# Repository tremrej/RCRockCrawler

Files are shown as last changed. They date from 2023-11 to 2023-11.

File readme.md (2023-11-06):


# RockCrawler
This is a remix version of an RC Rock Crawler that I found on Thingiverse.
The original model got deleted since then. So I included the original here.
The remix was first publish in Thingiverse at [Remix Rc Rock Crawler, new gearbox](https://www.thingiverse.com/thing:5236263).
I modified the gearbox to make it slower, hence with more torque.

General instruction:

1. Make sure the printer is well calibrated. Specifically the extruder. The extrusion factor, also know as the extrusion multiplier, will have a big impact on the way the pieces fits together. I personnaly use that guide before using a new filament: [Extrusion Multiplier](https://ellis3dp.com/Print-Tuning-Guide/articles/extrusion_multiplier.html)
2. Print every pieces in PLA.
3. Print the shock in PETG to get more flexibility.
4. If you decide to print the tires print them in TPU, the softest one you can find. The grip is not very good with printed tires. For better grip you can buy the tires. In that case print the wheel part wheel_26_5mm.stl.
4. If the screws tend to break the plastic part you can enlarge the hole with a drill bit.
4. Use plenty of light grease in the gear box
5. Use a bit of light grease in the wheel hub.
6. If the center drive shaft keep falling off you can print this longer one: Center_Drive_Shaft_P2_15.55mm.stl.
7. I provided a longer shock shock_46mm_stl. The short version tend to keep the car a bit low.

Video:

1. [In action](https://youtu.be/3EBpf9YP5C4)
2. [Showing the shock](https://youtu.be/YSYngEb9dG8)
3. [Gearbox assembly](https://youtu.be/KAkp_eB5qdQ)

I found a link to the original video from the original designer:

1. [Make an RC Rock Crawler - Part 1](https://www.youtube.com/watch?v=WgZuojB2sF8&t=138s)
2. [Make an RC Rock Crawler - Part 2](https://www.youtube.com/watch?v=jjvKoB2oO8Q&t=319s)

Documentation generated by the OpenSCAD library [NopSCADlib](https://github.com/nophead/NopSCADlib/tree/master).

License: [Creative Commons - Attribution - Share Alike](https://creativecommons.org/licenses/by-sa/3.0/).

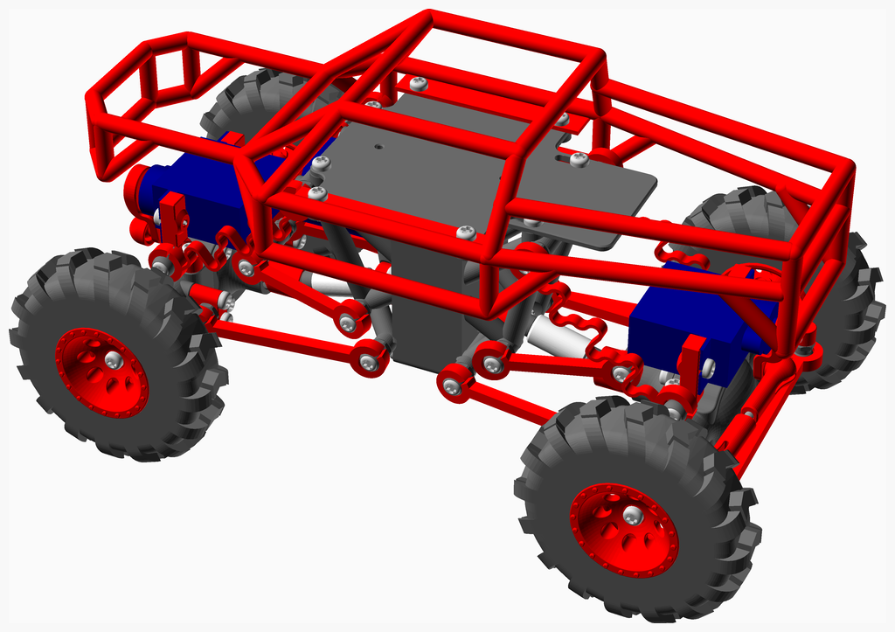
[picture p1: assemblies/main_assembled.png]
Main Assembly


<span></span>

---
## Table of Contents
1. [Parts list](#Parts_list)
1. [Wheel Left Assembly](#wheel_left_assembly)
1. [Wheel Right Assembly](#wheel_right_assembly)
1. [Drive Shaft Assembly](#drive_shaft_assembly)
1. [Servo Control Link Assembly](#Servo_control_link_assembly)
1. [Hub R Assembly](#Hub_R_assembly)
1. [Hub L Assembly](#Hub_L_assembly)
1. [Axle Part1 1 R Assembly](#Axle_part1_1_R_assembly)
1. [Axle Part1 1 L Assembly](#Axle_part1_1_L_assembly)
1. [G34 Assembly](#G34_assembly)
1. [Axle Part1 Assembly](#Axle_part1_assembly)
1. [Axle Part2 Assembly](#Axle_part2_assembly)
1. [Axle Part3 Assembly](#Axle_part3_assembly)
1. [Axle Part4 Assembly](#Axle_part4_assembly)
1. [Axle Part5 Assembly](#Axle_part5_assembly)
1. [Axle Part6 Assembly](#Axle_part6_assembly)
1. [Axle Part7 Assembly](#Axle_part7_assembly)
1. [Axle Final Assembly](#Axle_final_assembly)
1. [GearBox Part1 Assembly](#gearBox_part1_assembly)
1. [GearBox Part2 Assembly](#gearBox_part2_assembly)
1. [GearBox Part3 Assembly](#gearBox_part3_assembly)
1. [GearBox Part4 Assembly](#gearBox_part4_assembly)
1. [GearBox Part5 Assembly](#gearBox_part5_assembly)
1. [GearBox Part6 Assembly](#gearBox_part6_assembly)
1. [GearBox Part7 Assembly](#gearBox_part7_assembly)
1. [GearBox Final Assembly](#gearBox_final_assembly)
1. [Suspension Part1 Assembly](#suspension_part1_assembly)
1. [Suspension Part2 Assembly](#suspension_part2_assembly)
1. [Main Assembly](#main_assembly)

<span></span>
[Top](#TOP)

---

## Parts list
| <span style="writing-mode: vertical-rl; text-orientation: mixed;">2 x Axle&nbsp;Final</span> | <span style="writing-mode: vertical-rl; text-orientation: mixed;">GearBox&nbsp;Final</span> | <span style="writing-mode: vertical-rl; text-orientation: mixed;">Main</span> | <span style="writing-mode: vertical-rl; text-orientation: mixed;">TOTALS</span> |  |
|---:|---:|---:|---:|:---|
|  |  |  | | **Vitamins** |
| &nbsp;&nbsp;8&nbsp; | &nbsp;&nbsp;.&nbsp; | &nbsp;&nbsp;.&nbsp; |  &nbsp;&nbsp;8&nbsp; | &nbsp;&nbsp; Ball bearing MR128-2RS 8mm x 12mm x 3.5mm |
| &nbsp;&nbsp;6&nbsp; | &nbsp;&nbsp;2&nbsp; | &nbsp;&nbsp;.&nbsp; |  &nbsp;&nbsp;8&nbsp; | &nbsp;&nbsp; Ball bearing MR63ZZ 5mm x 8mm x 2.5mm |
| &nbsp;&nbsp;16&nbsp; | &nbsp;&nbsp;4&nbsp; | &nbsp;&nbsp;.&nbsp; |  &nbsp;&nbsp;20&nbsp; | &nbsp;&nbsp; Screw M2 pan self tap x  5mm |
| &nbsp;&nbsp;18&nbsp; | &nbsp;&nbsp;8&nbsp; | &nbsp;&nbsp;4&nbsp; |  &nbsp;&nbsp;30&nbsp; | &nbsp;&nbsp; Screw M2 pan self tap x  6mm |
| &nbsp;&nbsp;4&nbsp; | &nbsp;&nbsp;.&nbsp; | &nbsp;&nbsp;4&nbsp; |  &nbsp;&nbsp;8&nbsp; | &nbsp;&nbsp; Screw M2 pan self tap x  8mm |
| &nbsp;&nbsp;14&nbsp; | &nbsp;&nbsp;12&nbsp; | &nbsp;&nbsp;.&nbsp; |  &nbsp;&nbsp;26&nbsp; | &nbsp;&nbsp; Screw M2 pan self tap x 10mm |
| &nbsp;&nbsp;10&nbsp; | &nbsp;&nbsp;4&nbsp; | &nbsp;&nbsp;.&nbsp; |  &nbsp;&nbsp;14&nbsp; | &nbsp;&nbsp; Screw M2 pan self tap x 12mm |
| &nbsp;&nbsp;.&nbsp; | &nbsp;&nbsp;1&nbsp; | &nbsp;&nbsp;.&nbsp; |  &nbsp;&nbsp;1&nbsp; | &nbsp;&nbsp; Smooth rod 2mm x 10mm |
| &nbsp;&nbsp;2&nbsp; | &nbsp;&nbsp;.&nbsp; | &nbsp;&nbsp;.&nbsp; |  &nbsp;&nbsp;2&nbsp; | &nbsp;&nbsp; Threaded rod M2 x 10mm |
| &nbsp;&nbsp;2&nbsp; | &nbsp;&nbsp;.&nbsp; | &nbsp;&nbsp;.&nbsp; |  &nbsp;&nbsp;2&nbsp; | &nbsp;&nbsp;RC servo SG90 |
| &nbsp;&nbsp;.&nbsp; | &nbsp;&nbsp;1&nbsp; | &nbsp;&nbsp;.&nbsp; |  &nbsp;&nbsp;1&nbsp; | &nbsp;&nbsp;motor 130, 6 volts |
| &nbsp;&nbsp;80&nbsp; | &nbsp;&nbsp;32&nbsp; | &nbsp;&nbsp;8&nbsp; | &nbsp;&nbsp;120&nbsp; | &nbsp;&nbsp;Total vitamins count |
|  |  |  | | **3D printed parts** |
| &nbsp;&nbsp;2&nbsp; | &nbsp;&nbsp;.&nbsp; | &nbsp;&nbsp;.&nbsp; |  &nbsp;&nbsp;2&nbsp; | &nbsp;&nbsp;5_5_ball_Closed.stl |
| &nbsp;&nbsp;16&nbsp; | &nbsp;&nbsp;12&nbsp; | &nbsp;&nbsp;.&nbsp; |  &nbsp;&nbsp;28&nbsp; | &nbsp;&nbsp;5_5_ball_Open.stl |
| &nbsp;&nbsp;2&nbsp; | &nbsp;&nbsp;.&nbsp; | &nbsp;&nbsp;.&nbsp; |  &nbsp;&nbsp;2&nbsp; | &nbsp;&nbsp;Axle_Case_p1.stl |
| &nbsp;&nbsp;2&nbsp; | &nbsp;&nbsp;.&nbsp; | &nbsp;&nbsp;.&nbsp; |  &nbsp;&nbsp;2&nbsp; | &nbsp;&nbsp;Axle_Case_p2.stl |
| &nbsp;&nbsp;8&nbsp; | &nbsp;&nbsp;.&nbsp; | &nbsp;&nbsp;.&nbsp; |  &nbsp;&nbsp;8&nbsp; | &nbsp;&nbsp;Axle_Case_p3.stl |
| &nbsp;&nbsp;4&nbsp; | &nbsp;&nbsp;.&nbsp; | &nbsp;&nbsp;.&nbsp; |  &nbsp;&nbsp;4&nbsp; | &nbsp;&nbsp;Axle_Case_p4.stl |
| &nbsp;&nbsp;.&nbsp; | &nbsp;&nbsp;.&nbsp; | &nbsp;&nbsp;4&nbsp; |  &nbsp;&nbsp;4&nbsp; | &nbsp;&nbsp;Ball_Link_29mm.stl |
| &nbsp;&nbsp;.&nbsp; | &nbsp;&nbsp;.&nbsp; | &nbsp;&nbsp;4&nbsp; |  &nbsp;&nbsp;4&nbsp; | &nbsp;&nbsp;Ball_Link_41mm.stl |
| &nbsp;&nbsp;2&nbsp; | &nbsp;&nbsp;.&nbsp; | &nbsp;&nbsp;.&nbsp; |  &nbsp;&nbsp;2&nbsp; | &nbsp;&nbsp;Ball_Link_62mm.stl |
| &nbsp;&nbsp;2&nbsp; | &nbsp;&nbsp;2&nbsp; | &nbsp;&nbsp;.&nbsp; |  &nbsp;&nbsp;4&nbsp; | &nbsp;&nbsp;Center_Drive_Cup.stl |
| &nbsp;&nbsp;.&nbsp; | &nbsp;&nbsp;.&nbsp; | &nbsp;&nbsp;4&nbsp; |  &nbsp;&nbsp;4&nbsp; | &nbsp;&nbsp;Center_Drive_Shaft_P1.stl |
| &nbsp;&nbsp;.&nbsp; | &nbsp;&nbsp;.&nbsp; | &nbsp;&nbsp;2&nbsp; |  &nbsp;&nbsp;2&nbsp; | &nbsp;&nbsp;Center_Drive_Shaft_P2.stl |
| &nbsp;&nbsp;.&nbsp; | &nbsp;&nbsp;.&nbsp; | &nbsp;&nbsp;1&nbsp; |  &nbsp;&nbsp;1&nbsp; | &nbsp;&nbsp;Center_Drive_Shaft_P2_15_5mm.stl |
| &nbsp;&nbsp;4&nbsp; | &nbsp;&nbsp;.&nbsp; | &nbsp;&nbsp;.&nbsp; |  &nbsp;&nbsp;4&nbsp; | &nbsp;&nbsp;Drive_Cup.stl |
| &nbsp;&nbsp;4&nbsp; | &nbsp;&nbsp;.&nbsp; | &nbsp;&nbsp;.&nbsp; |  &nbsp;&nbsp;4&nbsp; | &nbsp;&nbsp;Drive_Shaft.stl |
| &nbsp;&nbsp;2&nbsp; | &nbsp;&nbsp;.&nbsp; | &nbsp;&nbsp;.&nbsp; |  &nbsp;&nbsp;2&nbsp; | &nbsp;&nbsp;G34_P14_p1.stl |
| &nbsp;&nbsp;2&nbsp; | &nbsp;&nbsp;.&nbsp; | &nbsp;&nbsp;.&nbsp; |  &nbsp;&nbsp;2&nbsp; | &nbsp;&nbsp;G34_P14_p2.stl |
| &nbsp;&nbsp;4&nbsp; | &nbsp;&nbsp;.&nbsp; | &nbsp;&nbsp;.&nbsp; |  &nbsp;&nbsp;4&nbsp; | &nbsp;&nbsp;Hub.stl |
| &nbsp;&nbsp;4&nbsp; | &nbsp;&nbsp;.&nbsp; | &nbsp;&nbsp;.&nbsp; |  &nbsp;&nbsp;4&nbsp; | &nbsp;&nbsp;Link_Closed_35mm.stl |
| &nbsp;&nbsp;.&nbsp; | &nbsp;&nbsp;1&nbsp; | &nbsp;&nbsp;.&nbsp; |  &nbsp;&nbsp;1&nbsp; | &nbsp;&nbsp;Motor_Holder.stl |
| &nbsp;&nbsp;2&nbsp; | &nbsp;&nbsp;.&nbsp; | &nbsp;&nbsp;.&nbsp; |  &nbsp;&nbsp;2&nbsp; | &nbsp;&nbsp;P14_G34.stl |
| &nbsp;&nbsp;4&nbsp; | &nbsp;&nbsp;.&nbsp; | &nbsp;&nbsp;.&nbsp; |  &nbsp;&nbsp;4&nbsp; | &nbsp;&nbsp;Servo_Holder.stl |
| &nbsp;&nbsp;2&nbsp; | &nbsp;&nbsp;.&nbsp; | &nbsp;&nbsp;.&nbsp; |  &nbsp;&nbsp;2&nbsp; | &nbsp;&nbsp;Servo_Horn.stl |
| &nbsp;&nbsp;.&nbsp; | &nbsp;&nbsp;.&nbsp; | &nbsp;&nbsp;4&nbsp; |  &nbsp;&nbsp;4&nbsp; | &nbsp;&nbsp;Wheel.stl |
| &nbsp;&nbsp;.&nbsp; | &nbsp;&nbsp;.&nbsp; | &nbsp;&nbsp;1&nbsp; |  &nbsp;&nbsp;1&nbsp; | &nbsp;&nbsp;body_v3.stl |
| &nbsp;&nbsp;.&nbsp; | &nbsp;&nbsp;1&nbsp; | &nbsp;&nbsp;.&nbsp; |  &nbsp;&nbsp;1&nbsp; | &nbsp;&nbsp;firstStageGear.stl |
| &nbsp;&nbsp;.&nbsp; | &nbsp;&nbsp;1&nbsp; | &nbsp;&nbsp;.&nbsp; |  &nbsp;&nbsp;1&nbsp; | &nbsp;&nbsp;frameBack_v2_1.stl |
| &nbsp;&nbsp;.&nbsp; | &nbsp;&nbsp;1&nbsp; | &nbsp;&nbsp;.&nbsp; |  &nbsp;&nbsp;1&nbsp; | &nbsp;&nbsp;frameFront_v2_1.stl |
| &nbsp;&nbsp;.&nbsp; | &nbsp;&nbsp;1&nbsp; | &nbsp;&nbsp;.&nbsp; |  &nbsp;&nbsp;1&nbsp; | &nbsp;&nbsp;gearMotor.stl |
| &nbsp;&nbsp;.&nbsp; | &nbsp;&nbsp;1&nbsp; | &nbsp;&nbsp;.&nbsp; |  &nbsp;&nbsp;1&nbsp; | &nbsp;&nbsp;gearboxBack_v2.stl |
| &nbsp;&nbsp;.&nbsp; | &nbsp;&nbsp;1&nbsp; | &nbsp;&nbsp;.&nbsp; |  &nbsp;&nbsp;1&nbsp; | &nbsp;&nbsp;gearboxFront_v2.stl |
| &nbsp;&nbsp;.&nbsp; | &nbsp;&nbsp;1&nbsp; | &nbsp;&nbsp;.&nbsp; |  &nbsp;&nbsp;1&nbsp; | &nbsp;&nbsp;plate_long_v2.stl |
| &nbsp;&nbsp;.&nbsp; | &nbsp;&nbsp;1&nbsp; | &nbsp;&nbsp;.&nbsp; |  &nbsp;&nbsp;1&nbsp; | &nbsp;&nbsp;secondStageGear.stl |
| &nbsp;&nbsp;.&nbsp; | &nbsp;&nbsp;.&nbsp; | &nbsp;&nbsp;4&nbsp; |  &nbsp;&nbsp;4&nbsp; | &nbsp;&nbsp;shock_43mm.stl |
| &nbsp;&nbsp;.&nbsp; | &nbsp;&nbsp;.&nbsp; | &nbsp;&nbsp;1&nbsp; |  &nbsp;&nbsp;1&nbsp; | &nbsp;&nbsp;shock_46mm.stl |
| &nbsp;&nbsp;.&nbsp; | &nbsp;&nbsp;.&nbsp; | &nbsp;&nbsp;4&nbsp; |  &nbsp;&nbsp;4&nbsp; | &nbsp;&nbsp;tire_v3.stl |
| &nbsp;&nbsp;.&nbsp; | &nbsp;&nbsp;.&nbsp; | &nbsp;&nbsp;1&nbsp; |  &nbsp;&nbsp;1&nbsp; | &nbsp;&nbsp;wheel_26_5mm.stl |
| &nbsp;&nbsp;66&nbsp; | &nbsp;&nbsp;23&nbsp; | &nbsp;&nbsp;30&nbsp; | &nbsp;&nbsp;119&nbsp; | &nbsp;&nbsp;Total 3D printed parts count |

<span></span>
[Top](#TOP)

---

## 2 x Wheel Left Assembly
### 3D Printed parts

| 2 x Wheel.stl | 2 x tire_v3.stl |
|---|---|
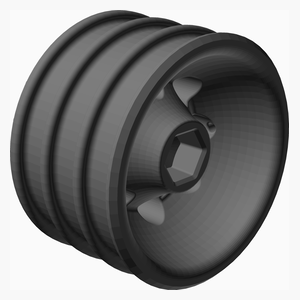
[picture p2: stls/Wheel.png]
Wheel.stl
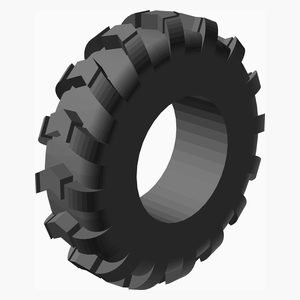
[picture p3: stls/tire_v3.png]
tire_v3.stl
|  |  

### Assembly instructions
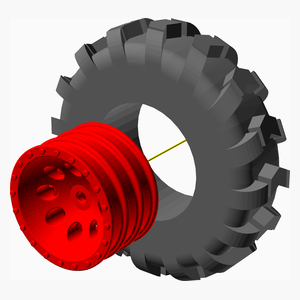
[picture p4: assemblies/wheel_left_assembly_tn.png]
wheel_left_assembly


1. Install the tire on the rim

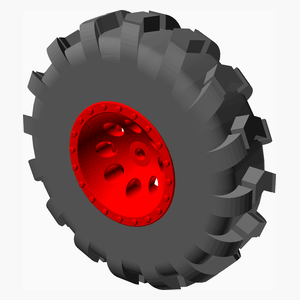
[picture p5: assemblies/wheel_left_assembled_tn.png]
wheel_left_assembled


<span></span>
[Top](#TOP)

---

## 2 x Wheel Right Assembly
### 3D Printed parts

| 2 x Wheel.stl | 2 x tire_v3.stl |
|---|---|
| Wheel.stl | tire_v3.stl 

### Assembly instructions
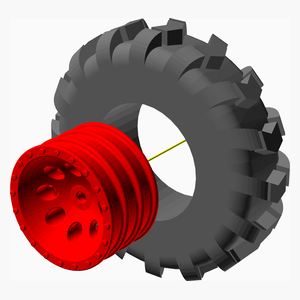
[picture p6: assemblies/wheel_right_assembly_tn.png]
wheel_right_assembly


1. Install the tire on the rim the thread oriented the other way compare to the wheel_left_assembly.

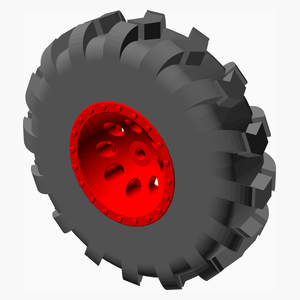
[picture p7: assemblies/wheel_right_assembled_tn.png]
wheel_right_assembled


<span></span>
[Top](#TOP)

---

## 2 x Drive Shaft Assembly
### 3D Printed parts

| 4 x Center_Drive_Shaft_P1.stl | 2 x Center_Drive_Shaft_P2.stl |
|---|---|
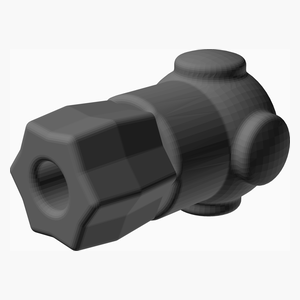
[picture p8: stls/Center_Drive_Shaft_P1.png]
Center_Drive_Shaft_P1.stl
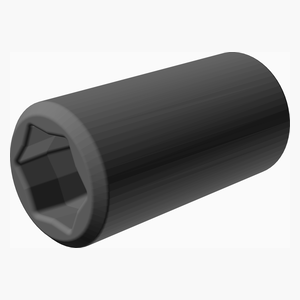
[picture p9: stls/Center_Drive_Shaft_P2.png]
Center_Drive_Shaft_P2.stl
|  |  

### Assembly instructions
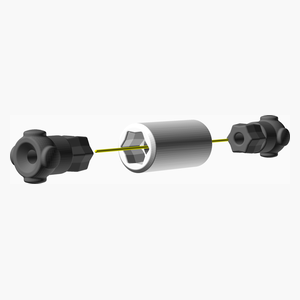
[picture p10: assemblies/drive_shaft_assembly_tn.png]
drive_shaft_assembly


1. It is a good idea to print the Center_Drive_Shaft_P2 in TPU. It makes the assembly a bit easier
2. Press fix both Center_Drive_Shaft_P1 into Center_Drive_Shaft_P2.

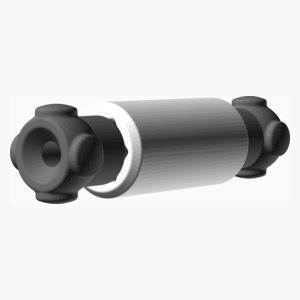
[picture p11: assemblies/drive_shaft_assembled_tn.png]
drive_shaft_assembled


<span></span>
[Top](#TOP)

---

## 2 x Servo Control Link Assembly
### Vitamins
|Qty|Description|
|---:|:---|
|2| Threaded rod M2 x 10mm|

### 3D Printed parts

| 4 x Link_Closed_35mm.stl |
|---|
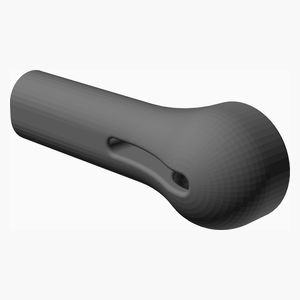
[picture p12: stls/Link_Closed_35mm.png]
Link_Closed_35mm.stl
|  

### Assembly instructions
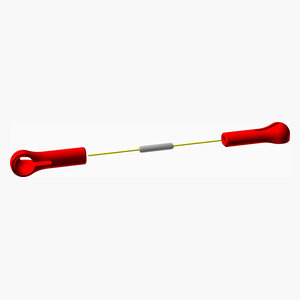
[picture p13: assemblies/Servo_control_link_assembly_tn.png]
Servo_control_link_assembly


1. Screw both Link_Closed_35mm on a 10 mm M2 threaded rod. Leave a gap of about 1 or 2 mm in the middle.

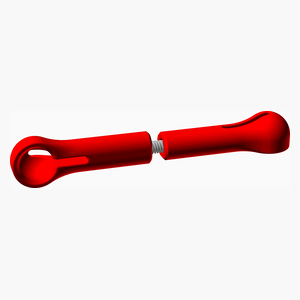
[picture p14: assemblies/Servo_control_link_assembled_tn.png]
Servo_control_link_assembled


<span></span>
[Top](#TOP)

---

## 2 x Hub R Assembly
### Vitamins
|Qty|Description|
|---:|:---|
|2| Ball bearing MR128-2RS 8mm x 12mm x 3.5mm|
|2| Ball bearing MR63ZZ 5mm x 8mm x 2.5mm|
|2| Screw M2 pan self tap x 10mm|

### 3D Printed parts

| 2 x 5_5_ball_Open.stl | 2 x Drive_Cup.stl | 2 x Hub.stl |
|---|---|---|
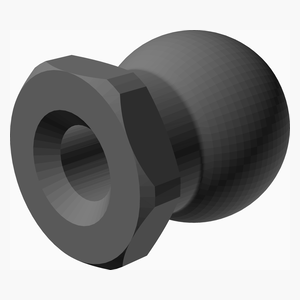
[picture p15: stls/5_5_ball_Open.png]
5_5_ball_Open.stl
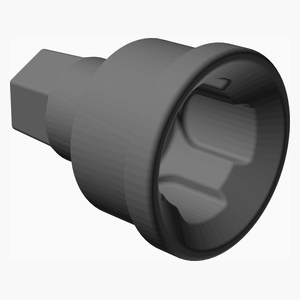
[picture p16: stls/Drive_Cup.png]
Drive_Cup.stl
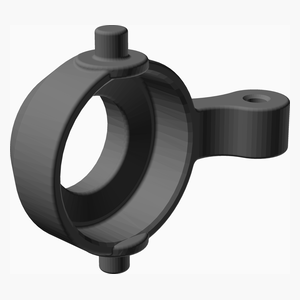
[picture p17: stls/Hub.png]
Hub.stl
|  |  |  

### Assembly instructions
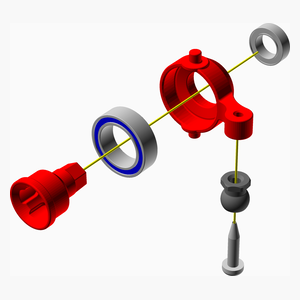
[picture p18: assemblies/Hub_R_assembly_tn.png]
Hub_R_assembly


1. Install a 5_5_ball_Open with a M2 self tapping screw 10 mm.
2. Install a bearing MR128 in the hub.
3. Install a bearing MR63 in the hub.
4. Install a Drive_Cup in the hub.

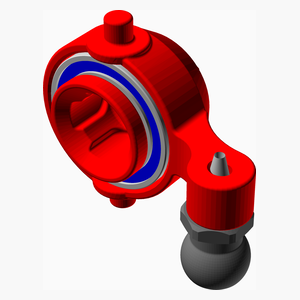
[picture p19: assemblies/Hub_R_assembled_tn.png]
Hub_R_assembled


<span></span>
[Top](#TOP)

---

## 2 x Hub L Assembly
### Vitamins
|Qty|Description|
|---:|:---|
|2| Ball bearing MR128-2RS 8mm x 12mm x 3.5mm|
|2| Ball bearing MR63ZZ 5mm x 8mm x 2.5mm|
|2| Screw M2 pan self tap x 12mm|

### 3D Printed parts

| 2 x 5_5_ball_Closed.stl | 2 x 5_5_ball_Open.stl | 2 x Drive_Cup.stl |
|---|---|---|
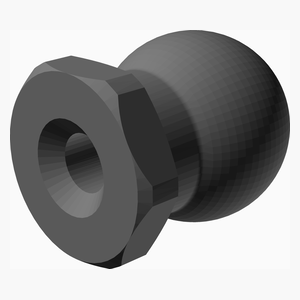
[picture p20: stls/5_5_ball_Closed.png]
5_5_ball_Closed.stl
|  | 5_5_ball_Open.stl | Drive_Cup.stl 

| 2 x Hub.stl |
|---|
| Hub.stl 

### Assembly instructions
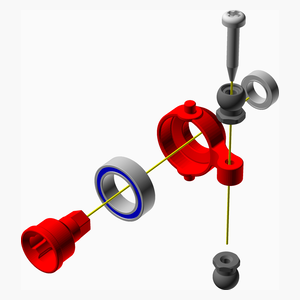
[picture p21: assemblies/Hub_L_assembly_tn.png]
Hub_L_assembly


1. Crew together a 5_5_ball_Open and a 5_5_ball_Closed with a M2 self tapping screw 12 mm.
2. Install a bearing MR128 in the Hub.
3. Install a bearing MR63 in the Hub.
4. Install a Drive_Cup in the Hub.

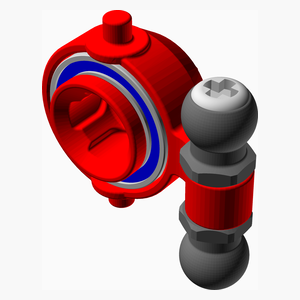
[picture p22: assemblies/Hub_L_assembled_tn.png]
Hub_L_assembled


<span></span>
[Top](#TOP)

---

## 2 x Axle Part1 1 R Assembly
### Vitamins
|Qty|Description|
|---:|:---|
|2| Screw M2 pan self tap x  8mm|

### 3D Printed parts

| 2 x 5_5_ball_Open.stl | 2 x Servo_Holder.stl |
|---|---|
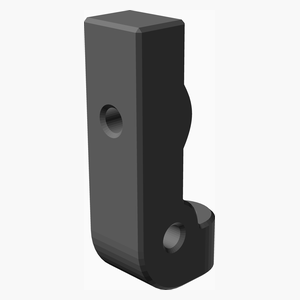
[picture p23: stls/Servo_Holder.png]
Servo_Holder.stl
| 5_5_ball_Open.stl |  

### Assembly instructions
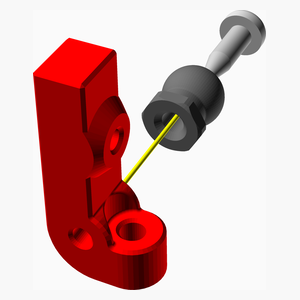
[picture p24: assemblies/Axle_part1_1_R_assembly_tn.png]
Axle_part1_1_R_assembly


1. Install a 5_5_ball_Closed on right side of a Servo_Holder using a M2 self tapping screw 8 mm.

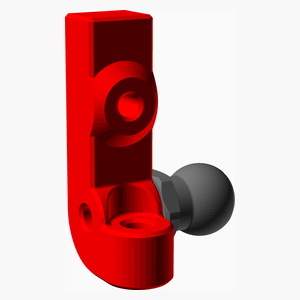
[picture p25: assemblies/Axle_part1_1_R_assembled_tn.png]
Axle_part1_1_R_assembled


<span></span>
[Top](#TOP)

---

## 2 x Axle Part1 1 L Assembly
### Vitamins
|Qty|Description|
|---:|:---|
|2| Screw M2 pan self tap x  8mm|

### 3D Printed parts

| 2 x 5_5_ball_Open.stl | 2 x Servo_Holder.stl |
|---|---|
| 5_5_ball_Open.stl | Servo_Holder.stl 

### Assembly instructions
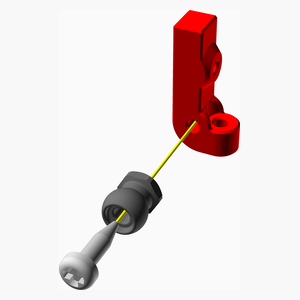
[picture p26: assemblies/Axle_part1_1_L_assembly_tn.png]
Axle_part1_1_L_assembly


1. Install a 5_5_ball_Closed on left side of a Servo_Holder using a M2 self tapping screw 8 mm.

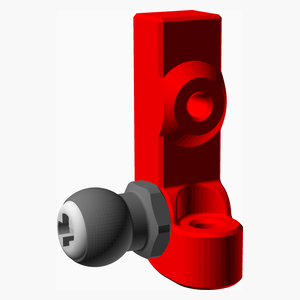
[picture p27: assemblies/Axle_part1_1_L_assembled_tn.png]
Axle_part1_1_L_assembled


<span></span>
[Top](#TOP)

---

## 2 x G34 Assembly
### Vitamins
|Qty|Description|
|---:|:---|
|4| Ball bearing MR128-2RS 8mm x 12mm x 3.5mm|
|2| Screw M2 pan self tap x  6mm|

### 3D Printed parts

| 2 x G34_P14_p1.stl | 2 x G34_P14_p2.stl |
|---|---|
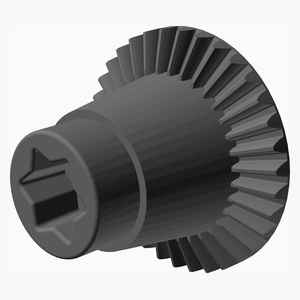
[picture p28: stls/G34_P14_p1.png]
G34_P14_p1.stl
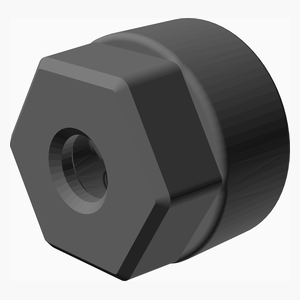
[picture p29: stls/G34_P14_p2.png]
G34_P14_p2.stl
|  |  

### Assembly instructions
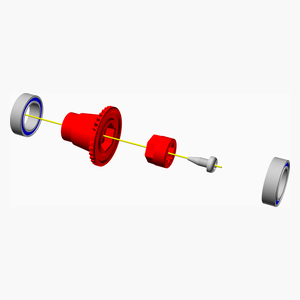
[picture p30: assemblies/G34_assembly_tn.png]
G34_assembly


1. Insert G34_P14_p2 in G34_P14_p1 using a M2 self tapping screw 8 mm.
2. Add the ball bearing MR128 at both ends.

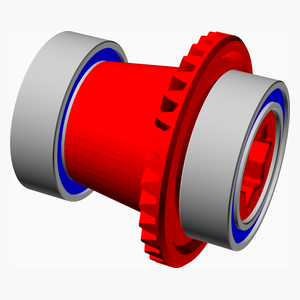
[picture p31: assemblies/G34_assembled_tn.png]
G34_assembled


<span></span>
[Top](#TOP)

---

## 4 x Axle Part1 Assembly
### Vitamins
|Qty|Description|
|---:|:---|
|4| Screw M2 pan self tap x 10mm|

### 3D Printed parts

| 4 x 5_5_ball_Open.stl | 4 x Axle_Case_p4.stl |
|---|---|
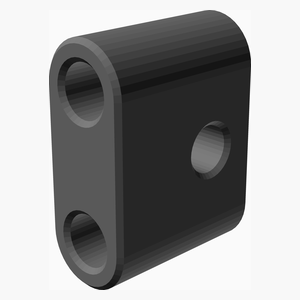
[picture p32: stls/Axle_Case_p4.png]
Axle_Case_p4.stl
| 5_5_ball_Open.stl |  

### Assembly instructions
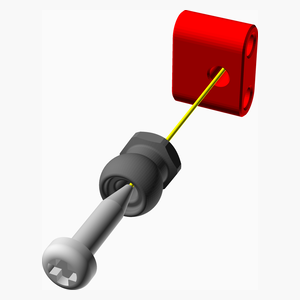
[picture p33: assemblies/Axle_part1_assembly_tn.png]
Axle_part1_assembly


1. Install a 5_5_ball_Closed on Axel_Case_p4 using a M2 self tapping screw 8 mm.

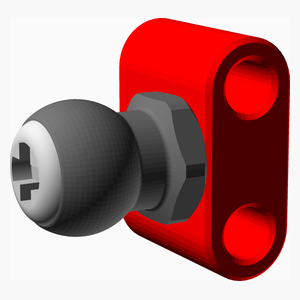
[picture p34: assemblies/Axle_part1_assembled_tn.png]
Axle_part1_assembled


<span></span>
[Top](#TOP)

---

## 2 x Axle Part2 Assembly
### Vitamins
|Qty|Description|
|---:|:---|
|8| Screw M2 pan self tap x 12mm|

### 3D Printed parts

| 2 x Axle_Case_p1.stl |
|---|
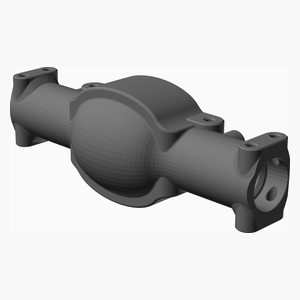
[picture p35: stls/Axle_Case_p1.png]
Axle_Case_p1.stl
|  

### Sub-assemblies

| 4 x Axle_part1_assembly |
|---|
| Axle_part1_assembled 

### Assembly instructions
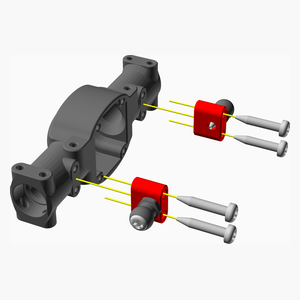
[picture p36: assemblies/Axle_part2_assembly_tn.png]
Axle_part2_assembly


1. Install both Axle_part1_assembly on the Axle_Case_p1 with 4 M2 self tapping screw 12 mm.

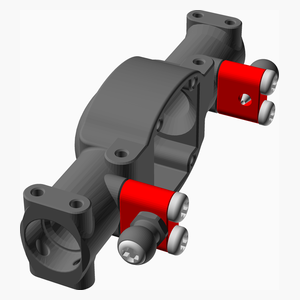
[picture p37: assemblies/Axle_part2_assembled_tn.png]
Axle_part2_assembled


<span></span>
[Top](#TOP)

---

## 2 x Axle Part3 Assembly
### Vitamins
|Qty|Description|
|---:|:---|
|2| Ball bearing MR63ZZ 5mm x 8mm x 2.5mm|
|8| Screw M2 pan self tap x  6mm|

### 3D Printed parts

| 2 x Axle_Case_p2.stl | 4 x Drive_Shaft.stl | 2 x P14_G34.stl |
|---|---|---|
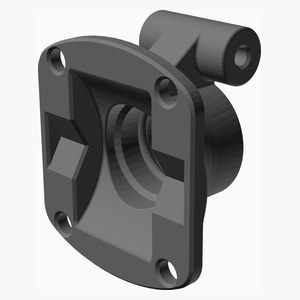
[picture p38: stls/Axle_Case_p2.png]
Axle_Case_p2.stl
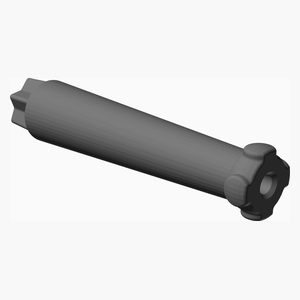
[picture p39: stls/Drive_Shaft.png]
Drive_Shaft.stl
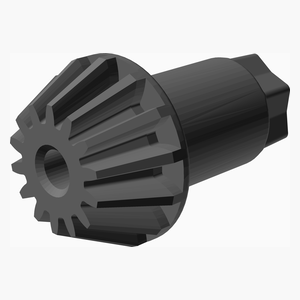
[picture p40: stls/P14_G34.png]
P14_G34.stl
|  |  |  

### Sub-assemblies

| 2 x Axle_part2_assembly | 2 x G34_assembly |
|---|---|
| Axle_part2_assembled | G34_assembled 

### Assembly instructions
Axle_part3_assembly

1. Insert G34_assembly in the axle.
2. Install ball bearing MR63 on P14_G34.
3. Install P14_G34 in Axle_Case_p2.
4. Fix Axle_Case_p2 on Axle_Case_p1 with 4 M2 self tapping screw 6 mm.
5. Insert both Drive_Shaft in axle. Note: there is no ball bearing on the shaft.

Axle_part3_assembled

<span></span>
[Top](#TOP)

---

## 2 x Axle Part4 Assembly
### Vitamins
|Qty|Description|
|---:|:---|
|8| Screw M2 pan self tap x 10mm|

### 3D Printed parts

| 4 x 5_5_ball_Open.stl |
|---|
| 5_5_ball_Open.stl 

### Sub-assemblies

| 2 x Axle_part1_1_L_assembly | 2 x Axle_part1_1_R_assembly | 2 x Axle_part3_assembly |
|---|---|---|
| Axle_part1_1_L_assembled | Axle_part1_1_R_assembled | Axle_part3_assembled 

### Assembly instructions
Axle_part4_assembly

1. Install two 5_5_ball_Closed on Axle_Case_p2 with M2 self tapping screw 10 mm.
2. Install the servo holders (Axle_part1_1_L_assembly & Axle_part1_1_R_assembly) on Axle_Case_p2 with 2 M2 self tapping screw 10 mm.

Axle_part4_assembled

<span></span>
[Top](#TOP)

---

## 2 x Axle Part5 Assembly
### Vitamins
|Qty|Description|
|---:|:---|
|16| Screw M2 pan self tap x  5mm|
|2| Screw M2 pan self tap x  6mm|

### 3D Printed parts

| 8 x Axle_Case_p3.stl | 2 x Center_Drive_Cup.stl |
|---|---|
| Axle_Case_p3.stl | Center_Drive_Cup.stl 

### Sub-assemblies

| 2 x Axle_part4_assembly | 2 x Hub_L_assembly | 2 x Hub_R_assembly |
|---|---|---|
| Axle_part4_assembled | Hub_L_assembled | Hub_R_assembled 

### Assembly instructions
Axle_part5_assembly

1. Install the Center_Drive_Cup in the Axle with a M2 self tapping screw 8 mm.
2. Install the Hub_L_assembly along with two Axle_Case_p3 with 4 M2 self tapping screw 5 mm
3. Install the Hub_R_assembly along with two Axle_Case_p3 with 4 M2 self tapping screw 5 mm

Axle_part5_assembled

<span></span>
[Top](#TOP)

---

## 2 x Axle Part6 Assembly
### Vitamins
|Qty|Description|
|---:|:---|
|4| Screw M2 pan self tap x  6mm|
|2|RC servo SG90|

### Sub-assemblies

| 2 x Axle_part5_assembly |
|---|
| Axle_part5_assembled 

### Assembly instructions
Axle_part6_assembly

1. Install the servo SG90 with 2 M2 self tapping screw 6 mm.

Axle_part6_assembled

<span></span>
[Top](#TOP)

---

## 2 x Axle Part7 Assembly
### Vitamins
|Qty|Description|
|---:|:---|
|2| Screw M2 pan self tap x  6mm|

### 3D Printed parts

| 2 x Servo_Horn.stl |
|---|
| Servo_Horn.stl 

### Sub-assemblies

| 2 x Axle_part6_assembly |
|---|
| Axle_part6_assembled 

### Assembly instructions
Axle_part7_assembly

1. Install the servo horn using the screw that came with the servo.

Axle_part7_assembled

<span></span>
[Top](#TOP)

---

## 2 x Axle Final Assembly
### 3D Printed parts

| 2 x Ball_Link_62mm.stl |
|---|
| Ball_Link_62mm.stl 

### Sub-assemblies

| 2 x Axle_part7_assembly | 2 x Servo_control_link_assembly |
|---|---|
| Axle_part7_assembled | Servo_control_link_assembled 

### Assembly instructions
Axle_final_assembly

1. Install a Servo_control_link_assembly from the servo horn to left hub.
2. Install a Ball_Link_62mm between the two hubs.

Axle_final_assembled

<span></span>
[Top](#TOP)

---

## GearBox Part1 Assembly
### Vitamins
|Qty|Description|
|---:|:---|
|1| Ball bearing MR63ZZ 5mm x 8mm x 2.5mm|
|4| Screw M2 pan self tap x  5mm|

### 3D Printed parts

| 1 x frameFront_v2_1.stl | 1 x gearboxFront_v2.stl |
|---|---|
| frameFront_v2_1.stl | gearboxFront_v2.stl 

### Assembly instructions
gearBox_part1_assembly

1. step 1

gearBox_part1_assembled

<span></span>
[Top](#TOP)

---

## GearBox Part2 Assembly
### Vitamins
|Qty|Description|
|---:|:---|
|1| Smooth rod 2mm x 10mm|

### 3D Printed parts

| 1 x firstStageGear.stl | 1 x secondStageGear.stl |
|---|---|
| firstStageGear.stl | secondStageGear.stl 

### Sub-assemblies

| 1 x gearBox_part1_assembly |
|---|
| gearBox_part1_assembled 

### Assembly instructions
gearBox_part2_assembly

1. Make sure the whole in firstStageGear is 2 mm using a 2 mm drill.
2. Make sure the whole in frameFront_v2_1 is 2mm using a 2 mm drill. Do not go through the case.
3. Put some grease on both side ot firstStageGear.
3. Insert the 2 mm rod in the firstStageGear. Then insert in the frameFront_v2_1. Make sure it turns freely.
4. Put some grease on both side ot secondStageGear.
5. Insert secondStageGear on top of firstStageGear.

gearBox_part2_assembled

<span></span>
[Top](#TOP)

---

## GearBox Part3 Assembly
### Vitamins
|Qty|Description|
|---:|:---|
|2| Screw M2 pan self tap x  6mm|
|1|motor 130, 6 volts|

### 3D Printed parts

| 1 x Motor_Holder.stl | 1 x gearMotor.stl |
|---|---|
| Motor_Holder.stl | gearMotor.stl 

### Sub-assemblies

| 1 x gearBox_part2_assembly |
|---|
| gearBox_part2_assembled 

### Assembly instructions
gearBox_part3_assembly

1. If your motor didn't come with a 8 thooht then insert the gearMotor onto the motor
2. Insert the motor. Make sure the gear are turning fine.
3. Install the Motor_Holder with 2 M2 self tapping screw 6 or 8 mm.

gearBox_part3_assembled

<span></span>
[Top](#TOP)

---

## GearBox Part4 Assembly
### Vitamins
|Qty|Description|
|---:|:---|
|1| Ball bearing MR63ZZ 5mm x 8mm x 2.5mm|

### 3D Printed parts

| 1 x gearboxBack_v2.stl |
|---|
| gearboxBack_v2.stl 

### Sub-assemblies

| 1 x gearBox_part3_assembly |
|---|
| gearBox_part3_assembled 

### Assembly instructions
gearBox_part4_assembly

gearBox_part4_assembled

<span></span>
[Top](#TOP)

---

## GearBox Part5 Assembly
### Vitamins
|Qty|Description|
|---:|:---|
|2| Screw M2 pan self tap x  6mm|

### 3D Printed parts

| 2 x Center_Drive_Cup.stl |
|---|
| Center_Drive_Cup.stl 

### Sub-assemblies

| 1 x gearBox_part4_assembly |
|---|
| gearBox_part4_assembled 

### Assembly instructions
gearBox_part5_assembly

1. Insert both Center_Drive_Cup with 2 M2 self tapping screw 6 mm.

gearBox_part5_assembled

<span></span>
[Top](#TOP)

---

## GearBox Part6 Assembly
### Vitamins
|Qty|Description|
|---:|:---|
|4| Screw M2 pan self tap x 12mm|

### 3D Printed parts

| 1 x frameBack_v2_1.stl |
|---|
| frameBack_v2_1.stl 

### Sub-assemblies

| 1 x gearBox_part5_assembly |
|---|
| gearBox_part5_assembled 

### Assembly instructions
gearBox_part6_assembly

1.Install the frameBack_v2_1 with 4 M2 self tapping screw 12 mm.

gearBox_part6_assembled

<span></span>
[Top](#TOP)

---

## GearBox Part7 Assembly
### Vitamins
|Qty|Description|
|---:|:---|
|4| Screw M2 pan self tap x  6mm|

### 3D Printed parts

| 1 x plate_long_v2.stl |
|---|
| plate_long_v2.stl 

### Sub-assemblies

| 1 x gearBox_part6_assembly |
|---|
| gearBox_part6_assembled 

### Assembly instructions
gearBox_part7_assembly

1.Install the frameBack_v2_1 with 4 M2 self tapping screw 12 mm.

gearBox_part7_assembled

<span></span>
[Top](#TOP)

---

## GearBox Final Assembly
### Vitamins
|Qty|Description|
|---:|:---|
|12| Screw M2 pan self tap x 10mm|

### 3D Printed parts

| 12 x 5_5_ball_Open.stl |
|---|
| 5_5_ball_Open.stl 

### Sub-assemblies

| 1 x gearBox_part7_assembly |
|---|
| gearBox_part7_assembled 

### Assembly instructions
gearBox_final_assembly

gearBox_final_assembled

<span></span>
[Top](#TOP)

---

## Suspension Part1 Assembly
### 3D Printed parts

| 4 x Ball_Link_29mm.stl | 4 x Ball_Link_41mm.stl |
|---|---|
| Ball_Link_29mm.stl | Ball_Link_41mm.stl 

### Sub-assemblies

| 2 x Axle_final_assembly | 2 x drive_shaft_assembly | 1 x gearBox_final_assembly |
|---|---|---|
| Axle_final_assembled | drive_shaft_assembled | gearBox_final_assembled 

### Assembly instructions
suspension_part1_assembly

1. Proceed with one end at a time.
2. Install the 2 Ball_Link_41mm
3. Install the drive_shaft_assembly
4. Install the 2 Ball_Link_29mm
5. Proceed with the other end.

suspension_part1_assembled

<span></span>
[Top](#TOP)

---

## Suspension Part2 Assembly
### 3D Printed parts

| 4 x shock_43mm.stl |
|---|
| shock_43mm.stl 

### Sub-assemblies

| 1 x suspension_part1_assembly |
|---|
| suspension_part1_assembled 

### Assembly instructions
suspension_part2_assembly

1. Install the shock. Pay attention to the opening at the ball joint: they should be facing up. This will make the shock bending downward when compressed.

suspension_part2_assembled

<span></span>
[Top](#TOP)

---

## Main Assembly
### Vitamins
|Qty|Description|
|---:|:---|
|4| Screw M2 pan self tap x  6mm|
|4| Screw M2 pan self tap x  8mm|

### 3D Printed parts

| 1 x Center_Drive_Shaft_P2_15_5mm.stl | 1 x body_v3.stl | 1 x shock_46mm.stl |
|---|---|---|
| Center_Drive_Shaft_P2_15_5mm.stl | body_v3.stl | shock_46mm.stl 

| 1 x wheel_26_5mm.stl |
|---|
| wheel_26_5mm.stl 

### Sub-assemblies

| 1 x suspension_part2_assembly | 2 x wheel_left_assembly | 2 x wheel_right_assembly |
|---|---|---|
| suspension_part2_assembled | wheel_left_assembled | wheel_right_assembled 

### Assembly instructions
main_assembly

1. Install the 4 wheel with M2 self tapping screw 8 mm.
2. Install the body with 4 M2 self tapping screw 5 mm.

main_assembled

<span></span>
[Top](#TOP)

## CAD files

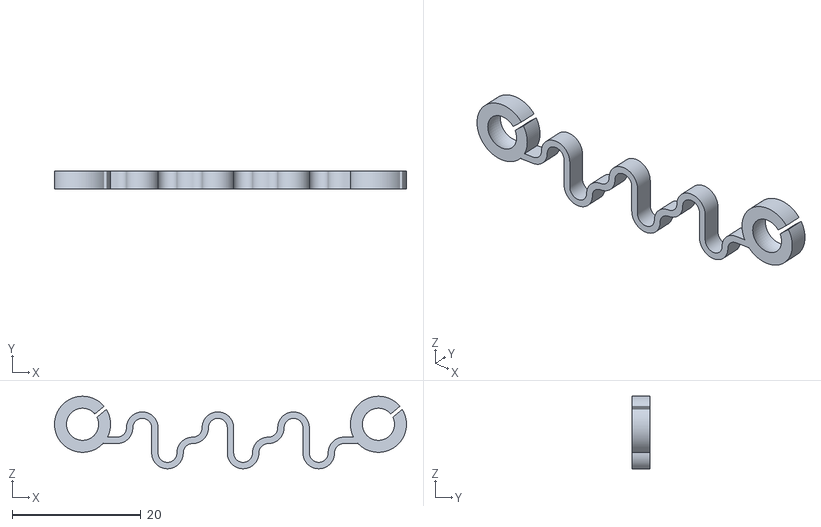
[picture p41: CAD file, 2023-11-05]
stls/shock_46mm.stl
54.7 x 2.83 x 11.3

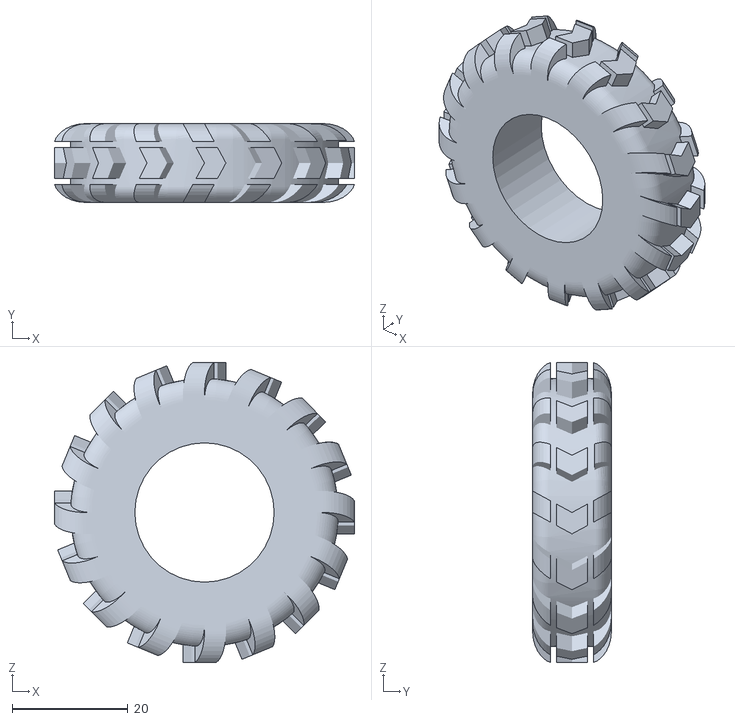
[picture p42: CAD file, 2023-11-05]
stls/tire_v3.stl
51.9 x 13.6 x 51.9

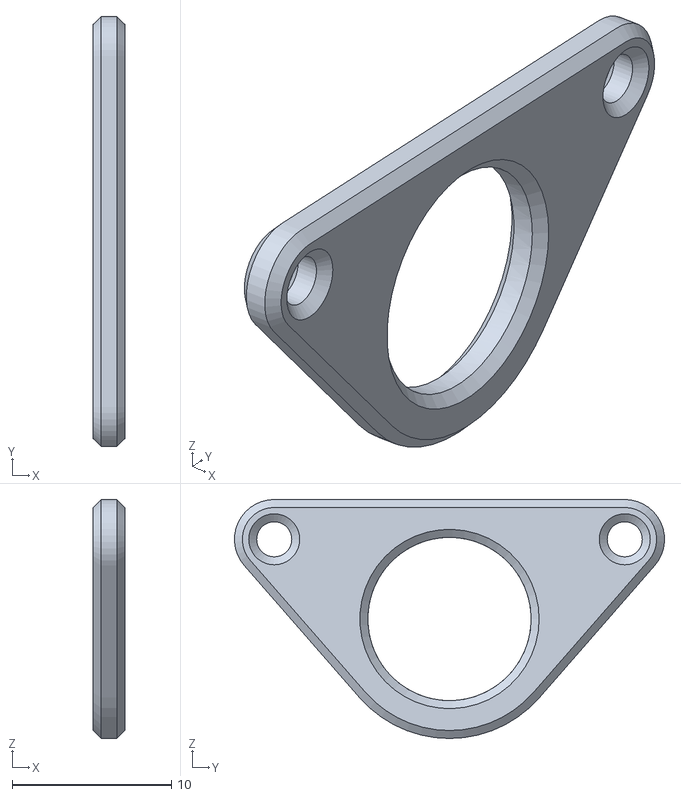
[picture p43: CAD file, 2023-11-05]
stls/Motor_Holder.stl
2.00 x 27.0 x 15.0

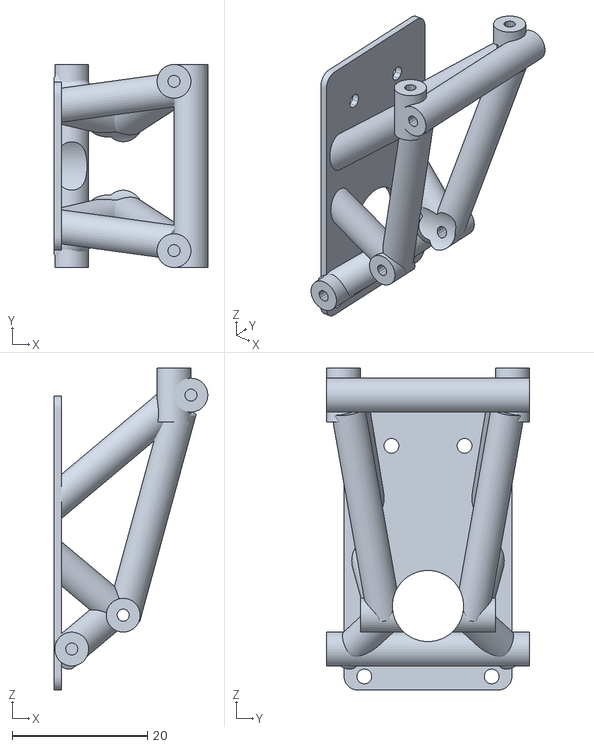
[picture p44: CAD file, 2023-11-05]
stls/frameBack_v2_1.stl
22.7 x 30.0 x 47.5

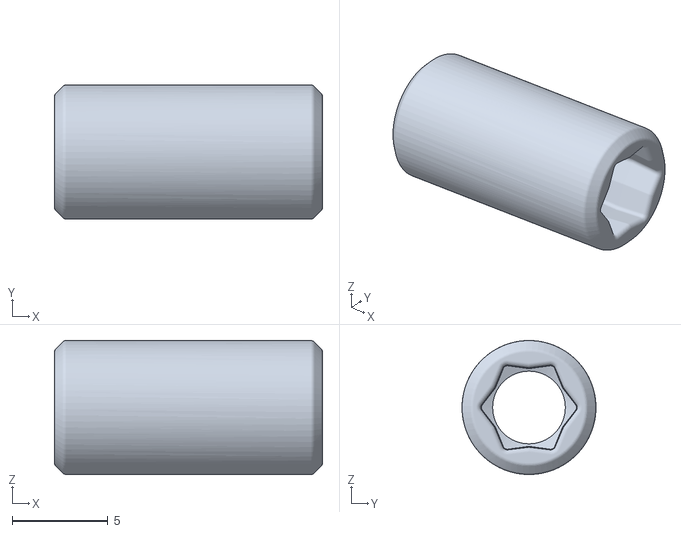
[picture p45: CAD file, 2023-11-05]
stls/Center_Drive_Shaft_P2.stl
14.0 x 7.00 x 7.00

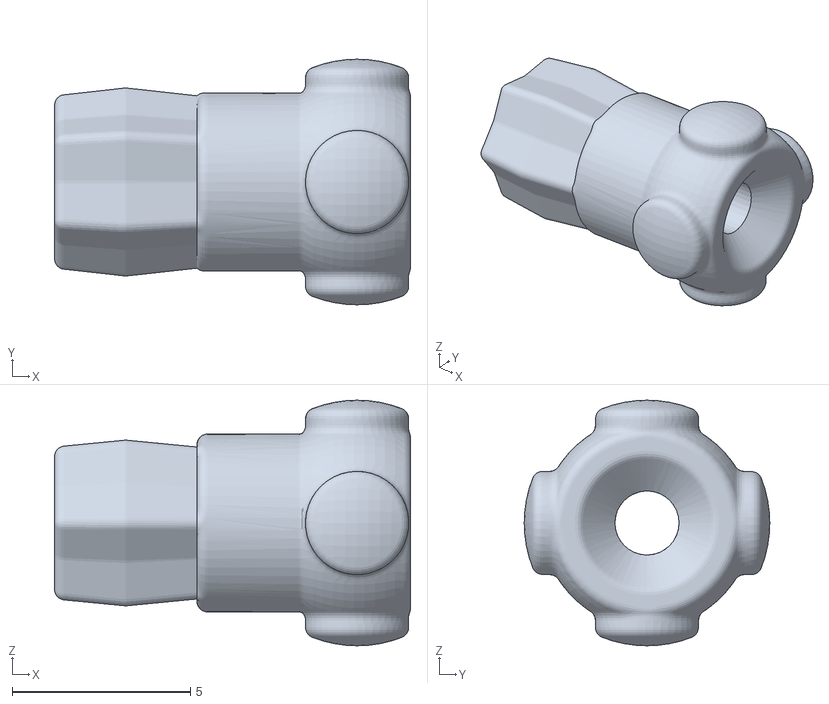
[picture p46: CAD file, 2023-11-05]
stls/Center_Drive_Shaft_P1.stl
10.0 x 6.90 x 6.90

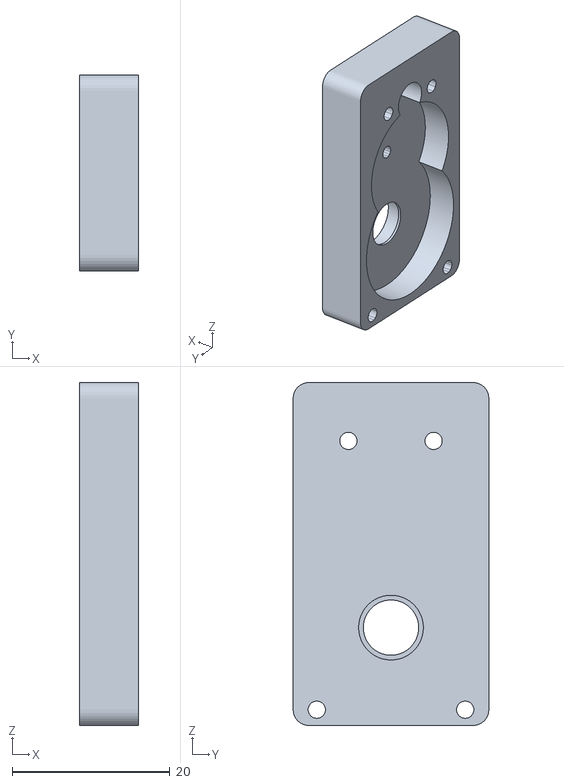
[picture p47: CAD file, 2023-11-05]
stls/gearboxBack_v2.stl
7.45 x 24.8 x 43.4

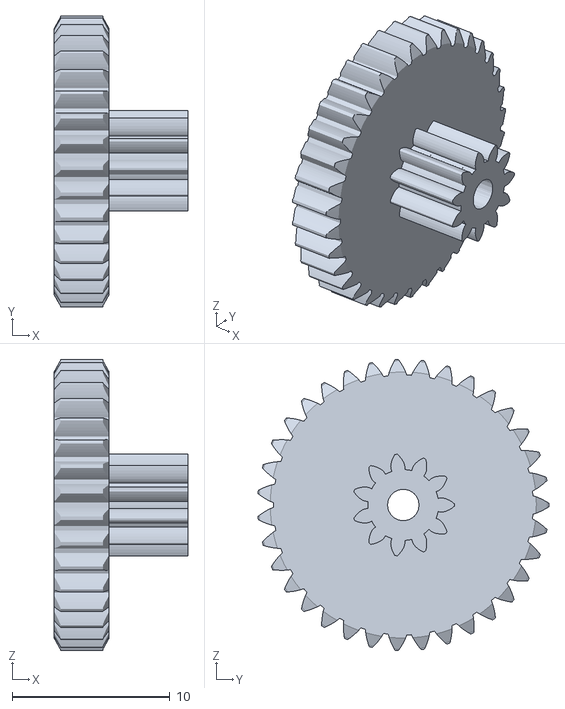
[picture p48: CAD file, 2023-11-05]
stls/firstStageGear.stl
8.50 x 18.5 x 18.5

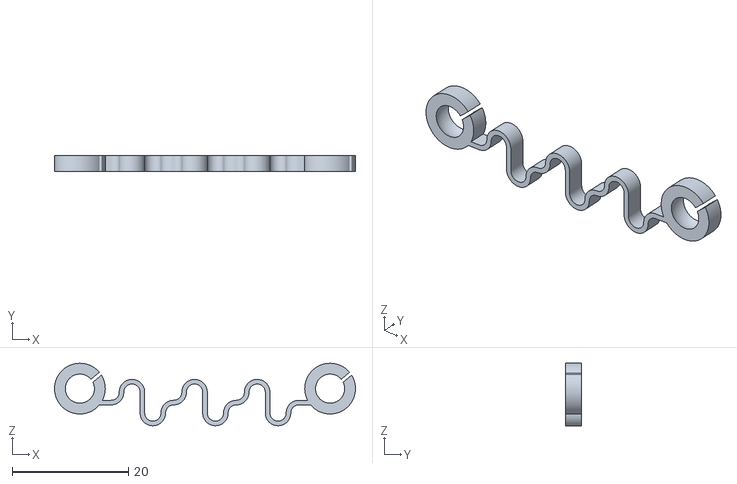
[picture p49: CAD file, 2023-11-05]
stls/shock_43mm.stl
51.7 x 2.83 x 10.7

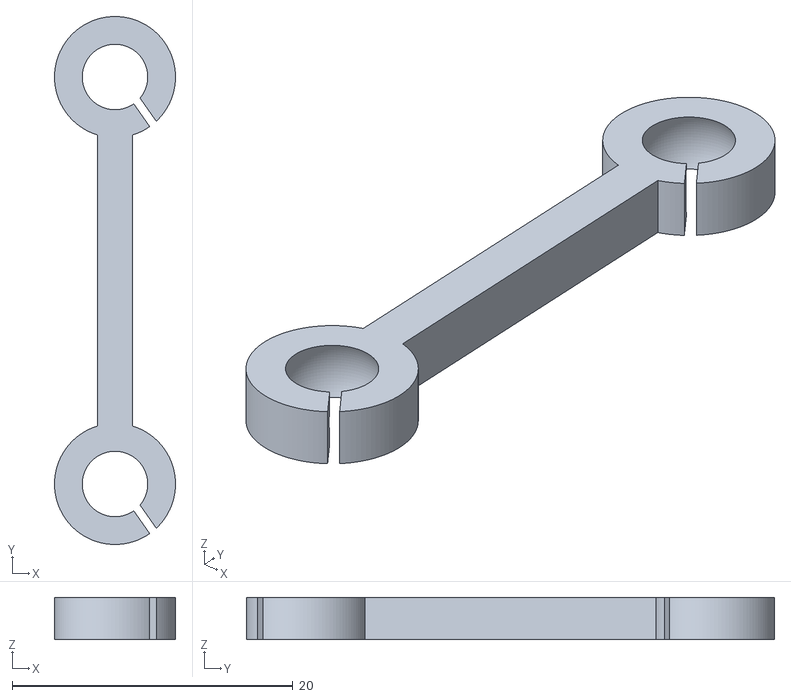
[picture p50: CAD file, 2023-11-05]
stls/Ball_Link_29mm.stl
8.62 x 37.6 x 3.01

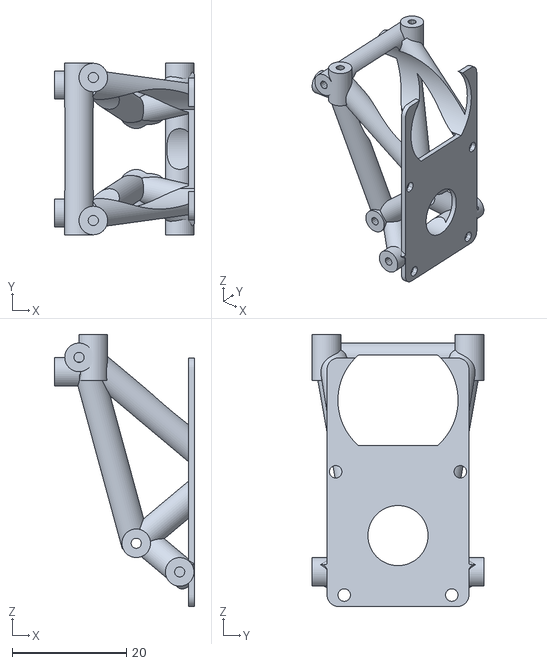
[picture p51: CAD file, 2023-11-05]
stls/frameFront_v2_1.stl
24.5 x 30.0 x 47.5

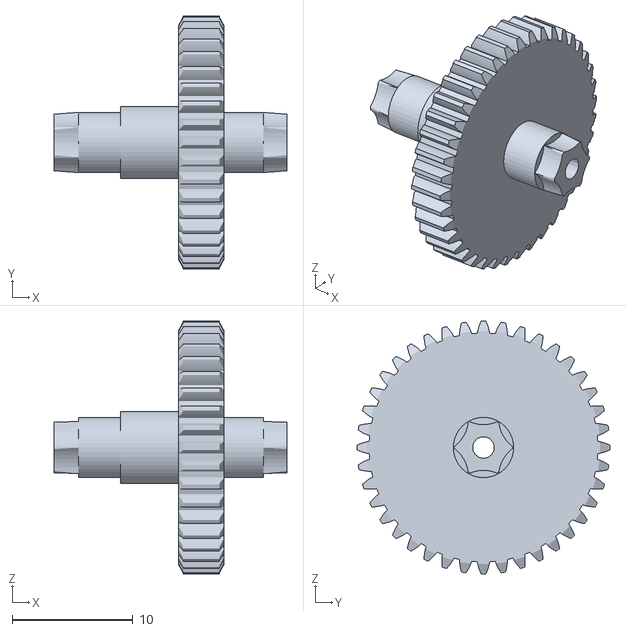
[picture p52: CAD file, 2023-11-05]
stls/secondStageGear.stl
19.3 x 21.0 x 21.0

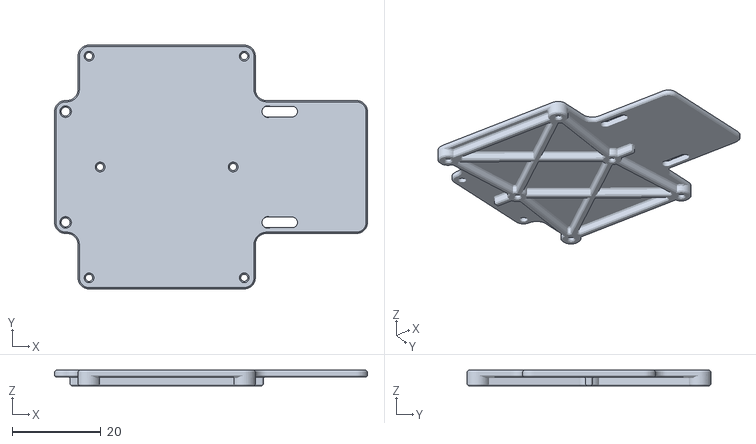
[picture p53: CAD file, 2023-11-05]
stls/plate_long_v2.stl
70.6 x 55.0 x 3.50

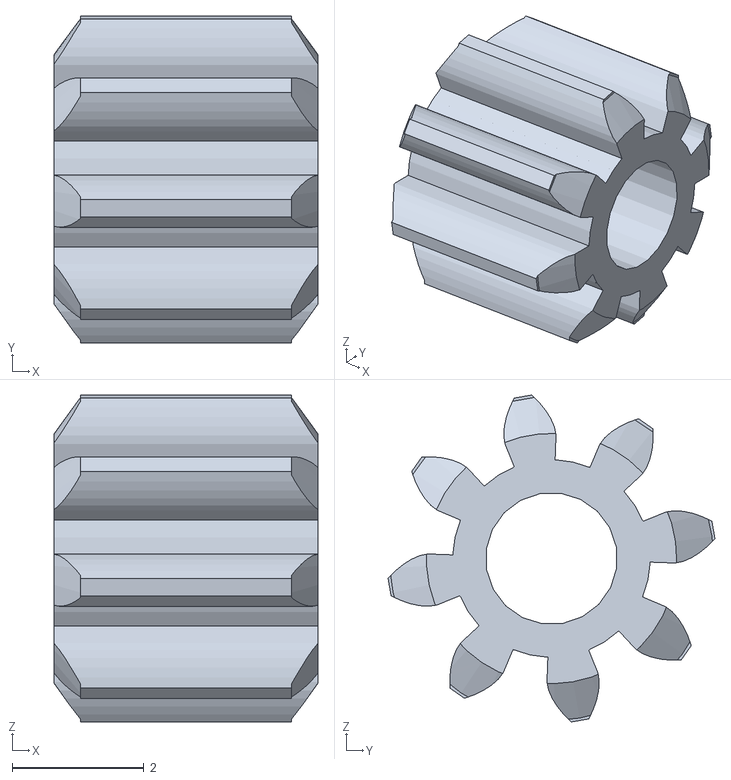
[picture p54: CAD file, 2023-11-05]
stls/gearMotor.stl
4.00 x 4.96 x 4.96

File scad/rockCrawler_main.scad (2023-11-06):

//
// Rc Rock Crawler with new gearbox.
// The original design got deleted from everywhere I could find it before: Thingiverse, Cult, MiniFactory.
// I updated the original file along with the new gearbox on Thingiverse, Cult and github.
//

//
//! This is a remix version of an RC Rock Crawler that I found on Thingiverse.
//! The original model got deleted since then. So I included the original here.
//! The remix was first publish in Thingiverse at [Remix Rc Rock Crawler, new gearbox](https://www.thingiverse.com/thing:5236263).
//! I modified the gearbox to make it slower, hence with more torque.
//!
//! General instruction:
//!
//! 1. Make sure the printer is well calibrated. Specifically the extruder. The extrusion factor, also know as the extrusion multiplier, will have a big impact on the way the pieces fits together. I personnaly use that guide before using a new filament: [Extrusion Multiplier](https://ellis3dp.com/Print-Tuning-Guide/articles/extrusion_multiplier.html)
//! 2. Print every pieces in PLA.
//! 3. Print the shock in PETG to get more flexibility.
//! 4. If you decide to print the tires print them in TPU, the softest one you can find. The grip is not very good with printed tires. For better grip you can buy the tires. In that case print the wheel part wheel_26_5mm.stl.
//! 4. If the screws tend to break the plastic part you can enlarge the hole with a drill bit.
//! 4. Use plenty of light grease in the gear box
//! 5. Use a bit of light grease in the wheel hub.
//! 6. If the center drive shaft keep falling off you can print this longer one: Center_Drive_Shaft_P2_15.55mm.stl.
//! 7. I provided a longer shock shock_46mm_stl. The short version tend to keep the car a bit low.
//! 
//!
//! Video:
//! 
//! 1. [In action](https://youtu.be/3EBpf9YP5C4)
//! 2. [Showing the shock](https://youtu.be/YSYngEb9dG8)
//! 3. [Gearbox assembly](https://youtu.be/KAkp_eB5qdQ)
//!
//! I found a link to the original video from the original designer:
//!
//! 1. [Make an RC Rock Crawler - Part 1](https://www.youtube.com/watch?v=WgZuojB2sF8&t=138s)
//! 2. [Make an RC Rock Crawler - Part 2](https://www.youtube.com/watch?v=jjvKoB2oO8Q&t=319s)
//!
//! Documentation generated by the OpenSCAD library [NopSCADlib](https://github.com/nophead/NopSCADlib/tree/master).
//!
//! License: [Creative Commons - Attribution - Share Alike](https://creativecommons.org/licenses/by-sa/3.0/).
//!

$show_threads = true;      // Set to false to speed up the processing
$extrusion_width = 0.4;
$layer_height = 0.2;
$pp1_colour = "dimgrey";
$pp2_colour = "red";
$pp3_colour = "darkblue";
$pp4_colour = "white";

include <NopSCADlib/core.scad>
use <NopSCADlib/utils/tube.scad>
use <NopSCADlib/utils/thread.scad>
use <NopSCADlib/vitamins/rod.scad>
use <NopSCADlib/vitamins/insert.scad>
include <NopSCADlib/vitamins/ball_bearings.scad>  // bb_width()
use <NopSCADlib/vitamins/ball_bearings.scad>
//use <MCAD/servos.scad>
$fn = 180;     // Uncomment to increase quality of stl

showAxle = false;
showttt = false;
showAssembly = true;


// The include ot MCAD library does't work with the script. Until I figure out what the problem is, I copied the function here.
module towerprosg90(position=undef, rotation=undef, screws = 0, axle_length = 0, cables=0)
{
	translate(position) rotate(rotation) {
        difference(){
            union()
            {
                translate([-5.9,-11.8/2,0]) cube([22.5,11.8,22.7]);
                translate([0,0,22.7-0.1]){
                    cylinder(d=11.8,h=4+0.1);
                    hull(){
                        translate([8.8-5/2,0,0]) cylinder(d=5,h=4+0.1);
                        cylinder(d=5,h=4+0.1);
                    }
                    translate([0,0,4]) cylinder(d=4.6,h=3.2);
                }
                translate([-4.7-5.9,-11.8/2,15.9]) cube([22.5+4.7*2, 11.8, 2.5]); 
            }
            //screw holes
            translate([-2.3-5.9,0,15.9+1.25]) cylinder(d=2,h=5, center=true);
            translate([-2.3-5.9-2,0,15.9+1.25]) cube([3,1.3,5], center=true);
            translate([2.3+22.5-5.9,0,15.9+1.25]) cylinder(d=2,h=5, center=true);
            translate([2.3+22.5-5.9+2,0,15.9+1.25]) cube([3,1.3,5], center=true);
        }
        if (axle_length > 0) {
            color("red", 0.3) translate([0,0,29.9/2]) cylinder(r=1, h=29.9+axle_length, center=true);
        }
        if (cables > 0) color("red", 0.3) translate([-12.4,-1.8,4.5]) cube([10,3.6,1.2]);
        if(screws > 0) color("red", 0.3) {
            translate([-2.3-5.9,0,15.9+1.25]) cylinder(d=2,h=10, center=true);
            translate([2.3+22.5-5.9,0,15.9+1.25]) cylinder(d=2,h=10, center=true);
        }
    }
    
}



module Axle_Case_p1_stl()
{
    stl("Axle_Case_p1");
    stl_colour(pp1_colour)
    translate([-10,-29.5,-11.5]) rotate([90,0,90]) import ("/home/rejeantremblay/Documents/openscad/RockCrawlerNewGearBox/Axle_Case_p1.STL");
}
module Axle_Case_p2_stl()
{
    stl("Axle_Case_p2");
    stl_colour(pp1_colour)
    translate([0,-9.6,-10.3]) rotate([90,0,0]) rotate([0,90,0]) import ("/home/rejeantremblay/Documents/openscad/RockCrawlerNewGearBox/Axle_Case_p2.STL");
}
module Axle_Case_p3_stl()
{
    stl("Axle_Case_p3");
    stl_colour(pp2_colour)
    translate([-5,0,0]) rotate([-90,0,0]) rotate([0,90,0]) import ("/home/rejeantremblay/Documents/openscad/RockCrawlerNewGearBox/Axle_Case_p3.STL");
}
module Axle_Case_p4_stl()
{
    stl("Axle_Case_p4");
    stl_colour(pp2_colour)
    translate([0,-2,-5]) rotate([90,0,0]) rotate([0,90,0]) import ("/home/rejeantremblay/Documents/openscad/RockCrawlerNewGearBox/Axle_Case_p4.STL");
}
module 5_5_ball_Closed_stl()
{
    stl("5_5_ball_Closed");
    stl_colour(pp1_colour)
    translate([0,2.7,-2.7]) rotate([0,0,-90]) import ("/home/rejeantremblay/Documents/openscad/RockCrawlerNewGearBox/5.5_ball_Closed.STL");
}
module 5_5_ball_Open_stl()
{
    stl("5_5_ball_Open");
    stl_colour(pp1_colour)
    translate([0,2.7,-2.7]) rotate([0,0,-90]) import ("/home/rejeantremblay/Documents/openscad/RockCrawlerNewGearBox/5.5_ball_Open.STL");
}

module G34_P14_p1_stl()
{
    stl("G34_P14_p1");
    stl_colour(pp2_colour)
    translate([0,-8.3,-8.3]) rotate([0,0,0]) import ("/home/rejeantremblay/Documents/openscad/RockCrawlerNewGearBox/G34_P14_p1.STL");
}
module G34_P14_p2_stl()
{
    stl("G34_P14_p2");
    stl_colour(pp2_colour)
    translate([0,-4,-4]) rotate([0,0,0]) import ("/home/rejeantremblay/Documents/openscad/RockCrawlerNewGearBox/G34_P14_p2.STL");
}
module P14_G34_stl()
{
    stl("P14_G34");
    stl_colour(pp2_colour)
    translate([-5.5,-4,-4]) rotate([0,0,0]) import ("/home/rejeantremblay/Documents/openscad/RockCrawlerNewGearBox/P14_G34.STL");
}
module Drive_Shaft_stl()
{
    stl("Drive_Shaft");
    stl_colour(pp2_colour)
    translate([-3,0,-3]) rotate([90,0,0]) import ("/home/rejeantremblay/Documents/openscad/RockCrawlerNewGearBox/Drive_Shaft.STL");
}
module Servo_Holder_stl()
{
    stl("Servo_Holder");
    stl_colour(pp2_colour)
    translate([0,-2.5,0]) rotate([0,0,90]) rotate([90,0,0]) import ("/home/rejeantremblay/Documents/openscad/RockCrawlerNewGearBox/Servo_Holder.STL");
}
module Hub_stl()
{
    stl("Hub");
    stl_colour(pp2_colour)
    translate([14.5,-5.5,9.0]) rotate([0,-90,0]) rotate([0,0,90]) import ("/home/rejeantremblay/Documents/openscad/RockCrawlerNewGearBox/Hub.STL");
}
module Drive_Cup_stl()
{
    stl("Drive_Cup");
    stl_colour(pp2_colour)
    translate([-4.5,0,4.5]) rotate([-90,0,0]) import ("/home/rejeantremblay/Documents/openscad/RockCrawlerNewGearBox/Drive_Cup.STL");
}
module Center_Drive_Cup_stl()
{
    stl("Center_Drive_Cup");
    stl_colour(pp2_colour)
    translate([0,-4.5,4.5]) rotate([0,90,0]) import ("/home/rejeantremblay/Documents/openscad/RockCrawlerNewGearBox/Center_Drive_Cup.STL");
}
module Servo_Horn_stl()
{
    stl("Servo_Horn");
    stl_colour(pp2_colour)
    translate([0,-5.3,-5.0]) rotate([0,0,90]) import ("/home/rejeantremblay/Documents/openscad/RockCrawlerNewGearBox/Servo_horn_-_5.5_4_ball.STL");
}
module Link_Closed_35mm_stl()
{
    stl("Link_Closed_35mm");
    stl_colour(pp2_colour)
    translate([-3.5,0,-3.5]) rotate([0,0,-90]) import ("/home/rejeantremblay/Documents/openscad/RockCrawlerNewGearBox/5.5_Link_Closed_35mm_C.STL");
}
module Ball_Link_62mm_stl()
{
    stl("Ball_Link_62mm");
    stl_colour(pp2_colour)
    translate([-3.5,0,-3.5]) rotate([0,0,-90]) import ("/home/rejeantremblay/Documents/openscad/RockCrawlerNewGearBox/ballLink_62.stl");
}
module Ball_Link_41mm_stl()
{
    stl("Ball_Link_41mm");
    stl_colour(pp2_colour)
    translate([-0,0,-3.5]) rotate([0,0,-90]) import ("/home/rejeantremblay/Documents/openscad/RockCrawlerNewGearBox/ballLink_41.stl");
}
module Ball_Link_29mm_stl()
{
    stl("Ball_Link_29mm");
    stl_colour(pp2_colour)
    translate([-0,0,-3.5]) rotate([0,0,-90]) import ("/home/rejeantremblay/Documents/openscad/RockCrawlerNewGearBox/ballLink_29.stl");
}
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

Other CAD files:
stls/gearboxFront_v2.stl
stls/Center_Drive_Shaft_P2_15_5mm.stl
stls/Axle_Case_p3.stl
stls/P14_G34.stl
stls/5_5_ball_Closed.stl
stls/5_5_ball_Open.stl
stls/Axle_Case_p4.stl
stls/Ball_Link_41mm.stl
stls/Ball_Link_62mm.stl
stls/Center_Drive_Cup.stl
stls/Drive_Shaft.stl
stls/G34_P14_p1.stl
stls/G34_P14_p2.stl
stls/Link_Closed_35mm.stl
stls/Servo_Holder.stl
stls/Servo_Horn.stl

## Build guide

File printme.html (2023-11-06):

# RockCrawler

This is a remix version of an RC Rock Crawler that I found on Thingiverse. The original model got deleted since then. So I included the original here. The remix was first publish in Thingiverse at Remix Rc Rock Crawler, new gearbox (https://www.thingiverse.com/thing:5236263). I modified the gearbox to make it slower, hence with more torque.

General instruction:

1. Make sure the printer is well calibrated. Specifically the extruder. The extrusion factor, also know as the extrusion multiplier, will have a big impact on the way the pieces fits together. I personnaly use that guide before using a new filament: Extrusion Multiplier (https://ellis3dp.com/Print-Tuning-Guide/articles/extrusion_multiplier.html)
2. Print every pieces in PLA.
3. Print the shock in PETG to get more flexibility.
4. If you decide to print the tires print them in TPU, the softest one you can find. The grip is not very good with printed tires. For better grip you can buy the tires. In that case print the wheel part wheel_26_5mm.stl.
5. If the screws tend to break the plastic part you can enlarge the hole with a drill bit.
6. Use plenty of light grease in the gear box
7. Use a bit of light grease in the wheel hub.
8. If the center drive shaft keep falling off you can print this longer one: Center_Drive_Shaft_P2_15.55mm.stl.
9. I provided a longer shock shock_46mm_stl. The short version tend to keep the car a bit low.

Video:

1. In action (https://youtu.be/3EBpf9YP5C4)
2. Showing the shock (https://youtu.be/YSYngEb9dG8)
3. Gearbox assembly (https://youtu.be/KAkp_eB5qdQ)

I found a link to the original video from the original designer:

1. Make an RC Rock Crawler - Part 1 (https://www.youtube.com/watch?v=WgZuojB2sF8&t=138s)
2. Make an RC Rock Crawler - Part 2 (https://www.youtube.com/watch?v=jjvKoB2oO8Q&t=319s)

Documentation generated by the OpenSCAD library NopSCADlib (https://github.com/nophead/NopSCADlib/tree/master).

License: Creative Commons - Attribution - Share Alike (https://creativecommons.org/licenses/by-sa/3.0/).

Main Assembly

## Table of Contents

1. Parts list
2. Wheel Left Assembly
3. Wheel Right Assembly
4. Drive Shaft Assembly
5. Servo Control Link Assembly
6. Hub R Assembly
7. Hub L Assembly
8. Axle Part1 1 R Assembly
9. Axle Part1 1 L Assembly
10. G34 Assembly
11. Axle Part1 Assembly
12. Axle Part2 Assembly
13. Axle Part3 Assembly
14. Axle Part4 Assembly
15. Axle Part5 Assembly
16. Axle Part6 Assembly
17. Axle Part7 Assembly
18. Axle Final Assembly
19. GearBox Part1 Assembly
20. GearBox Part2 Assembly
21. GearBox Part3 Assembly
22. GearBox Part4 Assembly
23. GearBox Part5 Assembly
24. GearBox Part6 Assembly
25. GearBox Part7 Assembly
26. GearBox Final Assembly
27. Suspension Part1 Assembly
28. Suspension Part2 Assembly
29. Main Assembly

## Parts list

2 x Axle Final | GearBox Final | Main | TOTALS
| | | | Vitamins
8 | . | . | 8 | Ball bearing MR128-2RS 8mm x 12mm x 3.5mm
6 | 2 | . | 8 | Ball bearing MR63ZZ 5mm x 8mm x 2.5mm
16 | 4 | . | 20 | Screw M2 pan self tap x 5mm
18 | 8 | 4 | 30 | Screw M2 pan self tap x 6mm
4 | . | 4 | 8 | Screw M2 pan self tap x 8mm
14 | 12 | . | 26 | Screw M2 pan self tap x 10mm
10 | 4 | . | 14 | Screw M2 pan self tap x 12mm
. | 1 | . | 1 | Smooth rod 2mm x 10mm
2 | . | . | 2 | Threaded rod M2 x 10mm
2 | . | . | 2 | RC servo SG90
. | 1 | . | 1 | motor 130, 6 volts
80 | 32 | 8 | 120 | Total vitamins count
| | | | 3D printed parts
2 | . | . | 2 | 5_5_ball_Closed.stl
16 | 12 | . | 28 | 5_5_ball_Open.stl
2 | . | . | 2 | Axle_Case_p1.stl
2 | . | . | 2 | Axle_Case_p2.stl
8 | . | . | 8 | Axle_Case_p3.stl
4 | . | . | 4 | Axle_Case_p4.stl
. | . | 4 | 4 | Ball_Link_29mm.stl
. | . | 4 | 4 | Ball_Link_41mm.stl
2 | . | . | 2 | Ball_Link_62mm.stl
2 | 2 | . | 4 | Center_Drive_Cup.stl
. | . | 4 | 4 | Center_Drive_Shaft_P1.stl
. | . | 2 | 2 | Center_Drive_Shaft_P2.stl
. | . | 1 | 1 | Center_Drive_Shaft_P2_15_5mm.stl
4 | . | . | 4 | Drive_Cup.stl
4 | . | . | 4 | Drive_Shaft.stl
2 | . | . | 2 | G34_P14_p1.stl
2 | . | . | 2 | G34_P14_p2.stl
4 | . | . | 4 | Hub.stl
4 | . | . | 4 | Link_Closed_35mm.stl
. | 1 | . | 1 | Motor_Holder.stl
2 | . | . | 2 | P14_G34.stl
4 | . | . | 4 | Servo_Holder.stl
2 | . | . | 2 | Servo_Horn.stl
. | . | 4 | 4 | Wheel.stl
. | . | 1 | 1 | body_v3.stl
. | 1 | . | 1 | firstStageGear.stl
. | 1 | . | 1 | frameBack_v2_1.stl
. | 1 | . | 1 | frameFront_v2_1.stl
. | 1 | . | 1 | gearMotor.stl
. | 1 | . | 1 | gearboxBack_v2.stl
. | 1 | . | 1 | gearboxFront_v2.stl
. | 1 | . | 1 | plate_long_v2.stl
. | 1 | . | 1 | secondStageGear.stl
. | . | 4 | 4 | shock_43mm.stl
. | . | 1 | 1 | shock_46mm.stl
. | . | 4 | 4 | tire_v3.stl
. | . | 1 | 1 | wheel_26_5mm.stl
66 | 23 | 30 | 119 | Total 3D printed parts count

## 2 x Wheel Left Assembly

### 3D Printed parts

2 x Wheel.stl | 2 x tire_v3.stl
Wheel.stl | tire_v3.stl

### Assembly instructions

wheel_left_assembly

1. Install the tire on the rim

wheel_left_assembled

## 2 x Wheel Right Assembly

### 3D Printed parts

2 x Wheel.stl | 2 x tire_v3.stl
Wheel.stl | tire_v3.stl

### Assembly instructions

wheel_right_assembly

1. Install the tire on the rim the thread oriented the other way compare to the wheel_left_assembly.

wheel_right_assembled

## 2 x Drive Shaft Assembly

### 3D Printed parts

4 x Center_Drive_Shaft_P1.stl | 2 x Center_Drive_Shaft_P2.stl
Center_Drive_Shaft_P1.stl | Center_Drive_Shaft_P2.stl

### Assembly instructions

drive_shaft_assembly

1. It is a good idea to print the Center_Drive_Shaft_P2 in TPU. It makes the assembly a bit easier
2. Press fix both Center_Drive_Shaft_P1 into Center_Drive_Shaft_P2.

drive_shaft_assembled

## 2 x Servo Control Link Assembly

### Vitamins

Qty | Description
2 | Threaded rod M2 x 10mm

### 3D Printed parts

4 x Link_Closed_35mm.stl

Link_Closed_35mm.stl

### Assembly instructions

Servo_control_link_assembly

1. Screw both Link_Closed_35mm on a 10 mm M2 threaded rod. Leave a gap of about 1 or 2 mm in the middle.

Servo_control_link_assembled

## 2 x Hub R Assembly

### Vitamins

Qty | Description
2 | Ball bearing MR128-2RS 8mm x 12mm x 3.5mm
2 | Ball bearing MR63ZZ 5mm x 8mm x 2.5mm
2 | Screw M2 pan self tap x 10mm

### 3D Printed parts

2 x 5_5_ball_Open.stl | 2 x Drive_Cup.stl | 2 x Hub.stl
5_5_ball_Open.stl | Drive_Cup.stl | Hub.stl

### Assembly instructions

Hub_R_assembly

1. Install a 5_5_ball_Open with a M2 self tapping screw 10 mm.
2. Install a bearing MR128 in the hub.
3. Install a bearing MR63 in the hub.
4. Install a Drive_Cup in the hub.

Hub_R_assembled

## 2 x Hub L Assembly

### Vitamins

Qty | Description
2 | Ball bearing MR128-2RS 8mm x 12mm x 3.5mm
2 | Ball bearing MR63ZZ 5mm x 8mm x 2.5mm
2 | Screw M2 pan self tap x 12mm

### 3D Printed parts

2 x 5_5_ball_Closed.stl | 2 x 5_5_ball_Open.stl | 2 x Drive_Cup.stl
5_5_ball_Closed.stl | 5_5_ball_Open.stl | Drive_Cup.stl

2 x Hub.stl

Hub.stl

### Assembly instructions

Hub_L_assembly

1. Crew together a 5_5_ball_Open and a 5_5_ball_Closed with a M2 self tapping screw 12 mm.
2. Install a bearing MR128 in the Hub.
3. Install a bearing MR63 in the Hub.
4. Install a Drive_Cup in the Hub.

Hub_L_assembled

## 2 x Axle Part1 1 R Assembly

### Vitamins

Qty | Description
2 | Screw M2 pan self tap x 8mm

### 3D Printed parts

2 x 5_5_ball_Open.stl | 2 x Servo_Holder.stl
5_5_ball_Open.stl | Servo_Holder.stl

### Assembly instructions

Axle_part1_1_R_assembly

1. Install a 5_5_ball_Closed on right side of a Servo_Holder using a M2 self tapping screw 8 mm.

Axle_part1_1_R_assembled

## 2 x Axle Part1 1 L Assembly

### Vitamins

Qty | Description
2 | Screw M2 pan self tap x 8mm

### 3D Printed parts

2 x 5_5_ball_Open.stl | 2 x Servo_Holder.stl
5_5_ball_Open.stl | Servo_Holder.stl

### Assembly instructions

Axle_part1_1_L_assembly

1. Install a 5_5_ball_Closed on left side of a Servo_Holder using a M2 self tapping screw 8 mm.

Axle_part1_1_L_assembled

## 2 x G34 Assembly

### Vitamins

Qty | Description
4 | Ball bearing MR128-2RS 8mm x 12mm x 3.5mm
2 | Screw M2 pan self tap x 6mm

### 3D Printed parts

2 x G34_P14_p1.stl | 2 x G34_P14_p2.stl
G34_P14_p1.stl | G34_P14_p2.stl

### Assembly instructions

G34_assembly

1. Insert G34_P14_p2 in G34_P14_p1 using a M2 self tapping screw 8 mm.
2. Add the ball bearing MR128 at both ends.

G34_assembled

## 4 x Axle Part1 Assembly

### Vitamins

Qty | Description
4 | Screw M2 pan self tap x 10mm

### 3D Printed parts

4 x 5_5_ball_Open.stl | 4 x Axle_Case_p4.stl
5_5_ball_Open.stl | Axle_Case_p4.stl

### Assembly instructions

Axle_part1_assembly

1. Install a 5_5_ball_Closed on Axel_Case_p4 using a M2 self tapping screw 8 mm.

Axle_part1_assembled

## 2 x Axle Part2 Assembly

### Vitamins

Qty | Description
8 | Screw M2 pan self tap x 12mm

### 3D Printed parts

2 x Axle_Case_p1.stl

Axle_Case_p1.stl

### Sub-assemblies

4 x Axle_part1_assembly

Axle_part1_assembled

### Assembly instructions

Axle_part2_assembly

1. Install both Axle_part1_assembly on the Axle_Case_p1 with 4 M2 self tapping screw 12 mm.

Axle_part2_assembled

## 2 x Axle Part3 Assembly

### Vitamins

Qty | Description
2 | Ball bearing MR63ZZ 5mm x 8mm x 2.5mm
8 | Screw M2 pan self tap x 6mm

### 3D Printed parts

2 x Axle_Case_p2.stl | 4 x Drive_Shaft.stl | 2 x P14_G34.stl
Axle_Case_p2.stl | Drive_Shaft.stl | P14_G34.stl

### Sub-assemblies

2 x Axle_part2_assembly | 2 x G34_assembly
Axle_part2_assembled | G34_assembled

### Assembly instructions

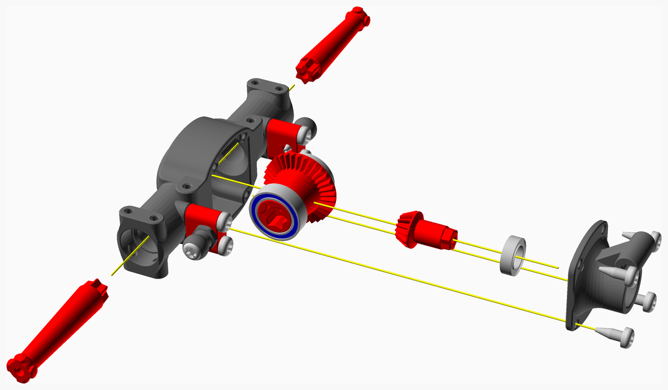
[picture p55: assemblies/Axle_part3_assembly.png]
Axle_part3_assembly


1. Insert G34_assembly in the axle.
2. Install ball bearing MR63 on P14_G34.
3. Install P14_G34 in Axle_Case_p2.
4. Fix Axle_Case_p2 on Axle_Case_p1 with 4 M2 self tapping screw 6 mm.
5. Insert both Drive_Shaft in axle. Note: there is no ball bearing on the shaft.

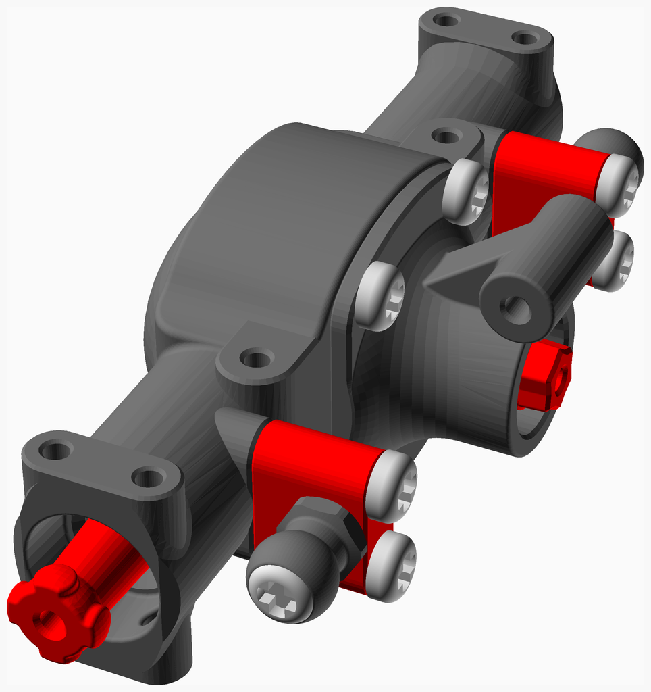
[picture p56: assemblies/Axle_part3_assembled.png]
Axle_part3_assembled


## 2 x Axle Part4 Assembly

### Vitamins

Qty | Description
8 | Screw M2 pan self tap x 10mm

### 3D Printed parts

4 x 5_5_ball_Open.stl

5_5_ball_Open.stl

### Sub-assemblies

2 x Axle_part1_1_L_assembly | 2 x Axle_part1_1_R_assembly | 2 x Axle_part3_assembly
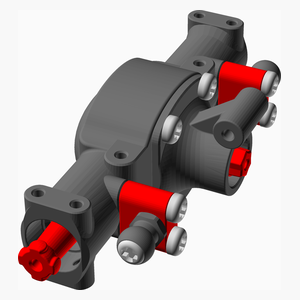
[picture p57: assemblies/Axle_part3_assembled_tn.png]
Axle_part3_assembled
Axle_part1_1_L_assembled | Axle_part1_1_R_assembled | 

### Assembly instructions

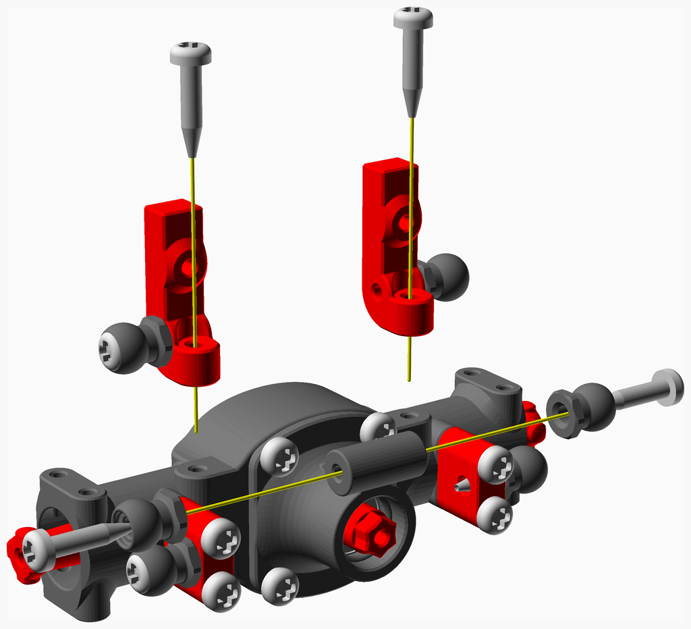
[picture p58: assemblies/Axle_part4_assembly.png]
Axle_part4_assembly


1. Install two 5_5_ball_Closed on Axle_Case_p2 with M2 self tapping screw 10 mm.
2. Install the servo holders (Axle_part1_1_L_assembly & Axle_part1_1_R_assembly) on Axle_Case_p2 with 2 M2 self tapping screw 10 mm.

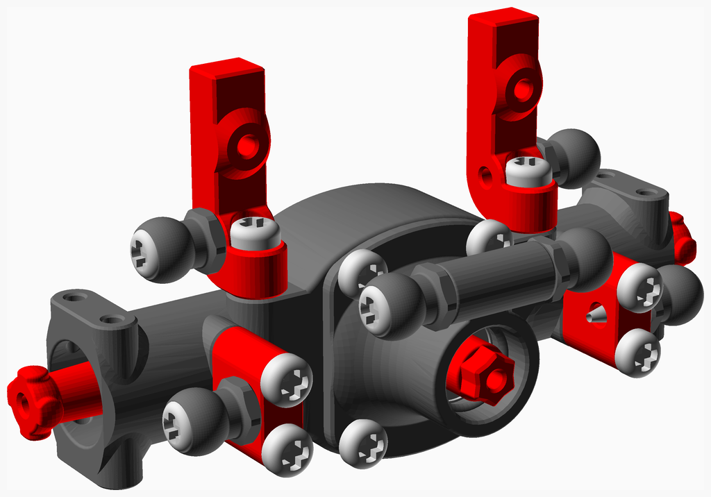
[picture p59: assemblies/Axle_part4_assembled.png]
Axle_part4_assembled


## 2 x Axle Part5 Assembly

### Vitamins

Qty | Description
16 | Screw M2 pan self tap x 5mm
2 | Screw M2 pan self tap x 6mm

### 3D Printed parts

8 x Axle_Case_p3.stl | 2 x Center_Drive_Cup.stl
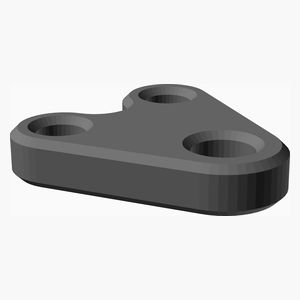
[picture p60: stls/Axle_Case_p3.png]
Axle_Case_p3.stl
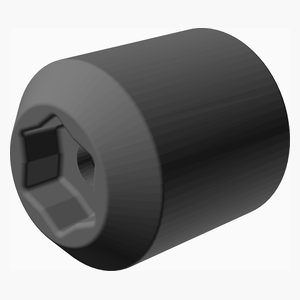
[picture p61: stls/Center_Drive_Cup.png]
Center_Drive_Cup.stl
 | 

### Sub-assemblies

2 x Axle_part4_assembly | 2 x Hub_L_assembly | 2 x Hub_R_assembly
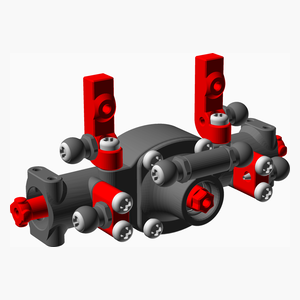
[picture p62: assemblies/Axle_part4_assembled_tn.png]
Axle_part4_assembled
 | Hub_L_assembled | Hub_R_assembled

### Assembly instructions

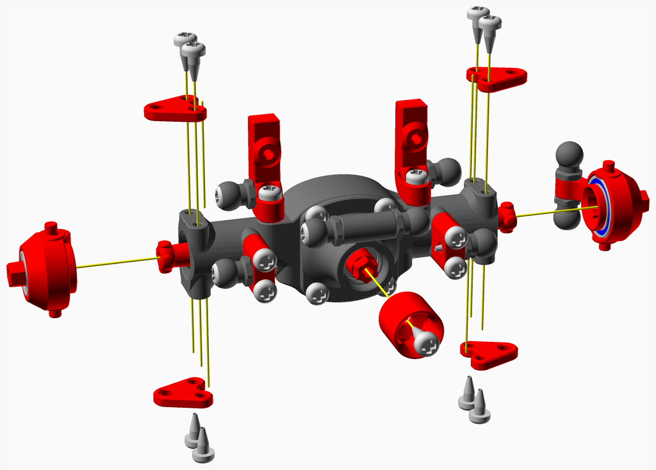
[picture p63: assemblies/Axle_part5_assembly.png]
Axle_part5_assembly


1. Install the Center_Drive_Cup in the Axle with a M2 self tapping screw 8 mm.
2. Install the Hub_L_assembly along with two Axle_Case_p3 with 4 M2 self tapping screw 5 mm
3. Install the Hub_R_assembly along with two Axle_Case_p3 with 4 M2 self tapping screw 5 mm

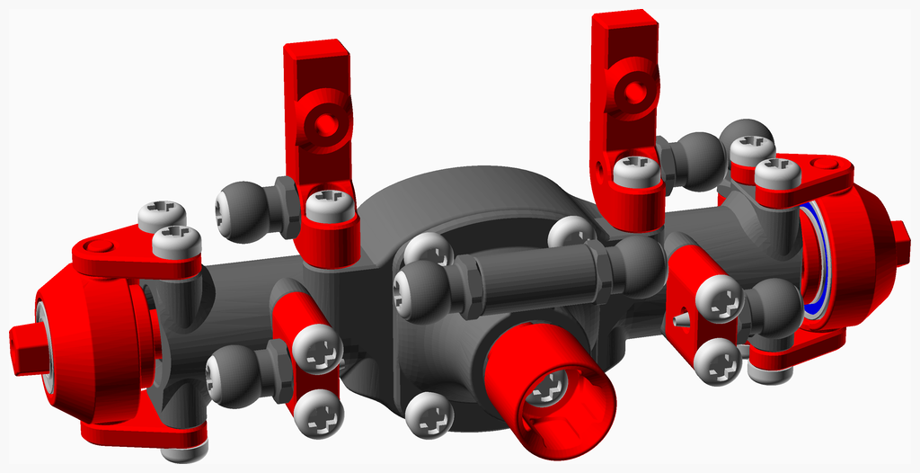
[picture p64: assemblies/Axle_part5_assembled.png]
Axle_part5_assembled


## 2 x Axle Part6 Assembly

### Vitamins

Qty | Description
4 | Screw M2 pan self tap x 6mm
2 | RC servo SG90

### Sub-assemblies

2 x Axle_part5_assembly

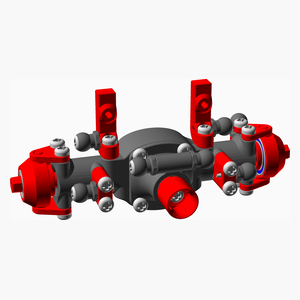
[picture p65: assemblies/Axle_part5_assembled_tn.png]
Axle_part5_assembled


### Assembly instructions

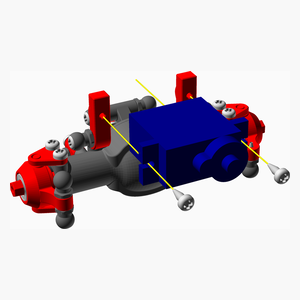
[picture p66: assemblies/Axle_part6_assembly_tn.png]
Axle_part6_assembly


1. Install the servo SG90 with 2 M2 self tapping screw 6 mm.

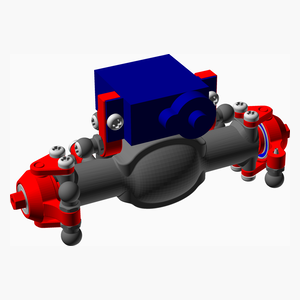
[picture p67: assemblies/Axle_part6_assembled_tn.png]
Axle_part6_assembled


## 2 x Axle Part7 Assembly

### Vitamins

Qty | Description
2 | Screw M2 pan self tap x 6mm

### 3D Printed parts

2 x Servo_Horn.stl

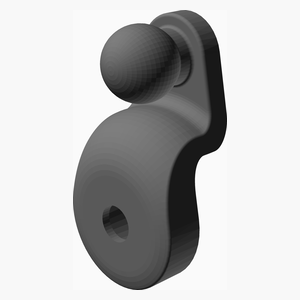
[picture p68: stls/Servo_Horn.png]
Servo_Horn.stl


### Sub-assemblies

2 x Axle_part6_assembly

Axle_part6_assembled

### Assembly instructions

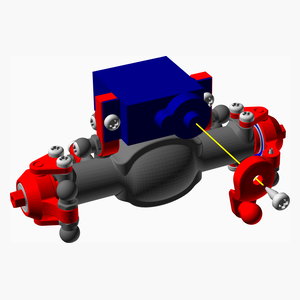
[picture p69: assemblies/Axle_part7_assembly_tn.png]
Axle_part7_assembly


1. Install the servo horn using the screw that came with the servo.

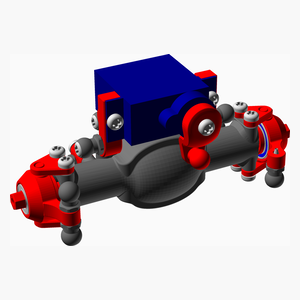
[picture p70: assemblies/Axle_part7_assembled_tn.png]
Axle_part7_assembled


## 2 x Axle Final Assembly

### 3D Printed parts

2 x Ball_Link_62mm.stl

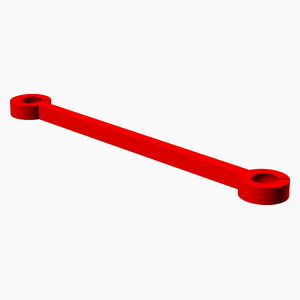
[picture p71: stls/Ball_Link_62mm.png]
Ball_Link_62mm.stl


### Sub-assemblies

2 x Axle_part7_assembly | 2 x Servo_control_link_assembly
Axle_part7_assembled | Servo_control_link_assembled

### Assembly instructions

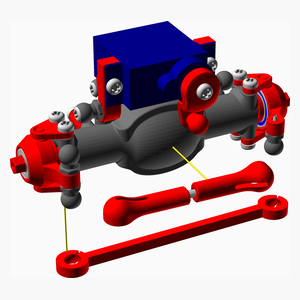
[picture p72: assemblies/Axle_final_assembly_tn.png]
Axle_final_assembly


1. Install a Servo_control_link_assembly from the servo horn to left hub.
2. Install a Ball_Link_62mm between the two hubs.

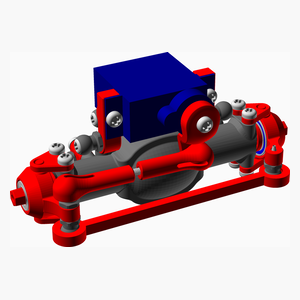
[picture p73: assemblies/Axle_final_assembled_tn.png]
Axle_final_assembled


## GearBox Part1 Assembly

### Vitamins

Qty | Description
1 | Ball bearing MR63ZZ 5mm x 8mm x 2.5mm
4 | Screw M2 pan self tap x 5mm

### 3D Printed parts

1 x frameFront_v2_1.stl | 1 x gearboxFront_v2.stl
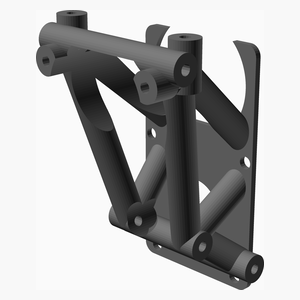
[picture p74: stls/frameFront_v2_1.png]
frameFront_v2_1.stl
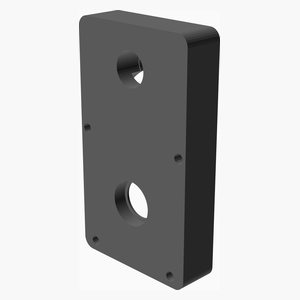
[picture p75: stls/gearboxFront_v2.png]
gearboxFront_v2.stl
 | 

### Assembly instructions

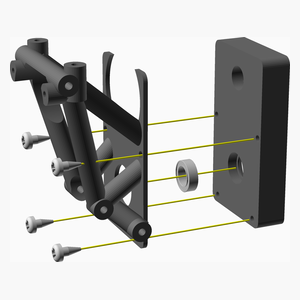
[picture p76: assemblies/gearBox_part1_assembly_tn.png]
gearBox_part1_assembly


1. step 1

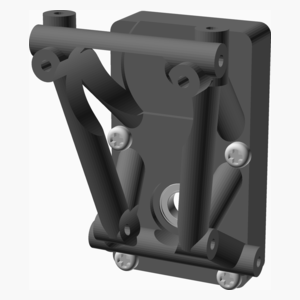
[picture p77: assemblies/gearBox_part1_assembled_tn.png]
gearBox_part1_assembled


## GearBox Part2 Assembly

### Vitamins

Qty | Description
1 | Smooth rod 2mm x 10mm

### 3D Printed parts

1 x firstStageGear.stl | 1 x secondStageGear.stl
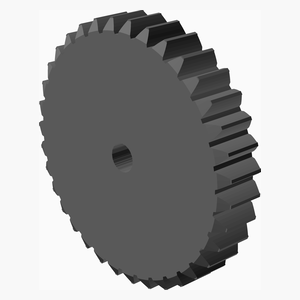
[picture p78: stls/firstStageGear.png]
firstStageGear.stl
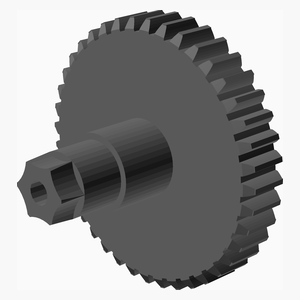
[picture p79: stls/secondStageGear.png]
secondStageGear.stl
 | 

### Sub-assemblies

1 x gearBox_part1_assembly

gearBox_part1_assembled

### Assembly instructions

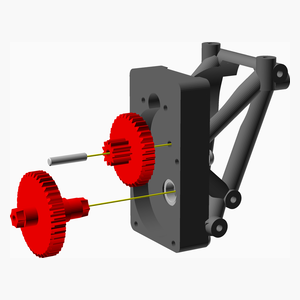
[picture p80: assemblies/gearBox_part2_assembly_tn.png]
gearBox_part2_assembly


1. Make sure the whole in firstStageGear is 2 mm using a 2 mm drill.
2. Make sure the whole in frameFront_v2_1 is 2mm using a 2 mm drill. Do not go through the case.
3. Put some grease on both side ot firstStageGear.
4. Insert the 2 mm rod in the firstStageGear. Then insert in the frameFront_v2_1. Make sure it turns freely.
5. Put some grease on both side ot secondStageGear.
6. Insert secondStageGear on top of firstStageGear.

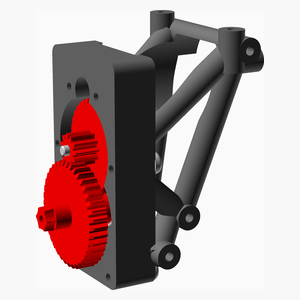
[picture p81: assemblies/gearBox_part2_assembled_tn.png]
gearBox_part2_assembled


## GearBox Part3 Assembly

### Vitamins

Qty | Description
2 | Screw M2 pan self tap x 6mm
1 | motor 130, 6 volts

### 3D Printed parts

1 x Motor_Holder.stl | 1 x gearMotor.stl
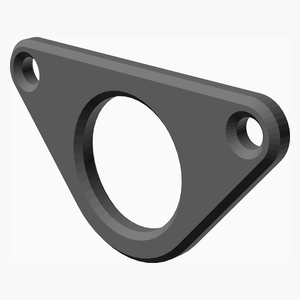
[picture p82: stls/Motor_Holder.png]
Motor_Holder.stl
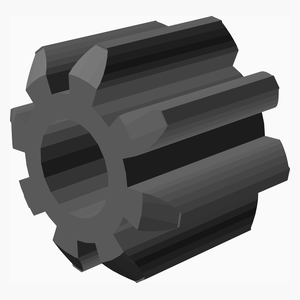
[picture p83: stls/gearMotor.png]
gearMotor.stl
 | 

### Sub-assemblies

1 x gearBox_part2_assembly

gearBox_part2_assembled

### Assembly instructions

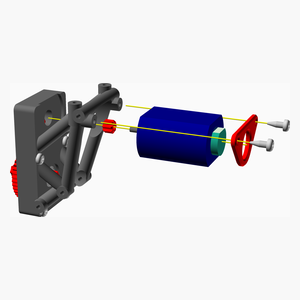
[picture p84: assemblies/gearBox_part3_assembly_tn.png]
gearBox_part3_assembly


1. If your motor didn't come with a 8 thooht then insert the gearMotor onto the motor
2. Insert the motor. Make sure the gear are turning fine.
3. Install the Motor_Holder with 2 M2 self tapping screw 6 or 8 mm.

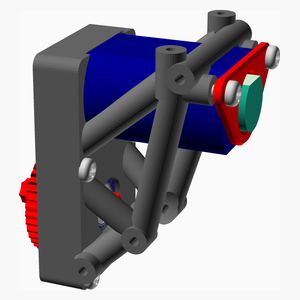
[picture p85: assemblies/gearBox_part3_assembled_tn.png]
gearBox_part3_assembled


## GearBox Part4 Assembly

### Vitamins

Qty | Description
1 | Ball bearing MR63ZZ 5mm x 8mm x 2.5mm

### 3D Printed parts

1 x gearboxBack_v2.stl

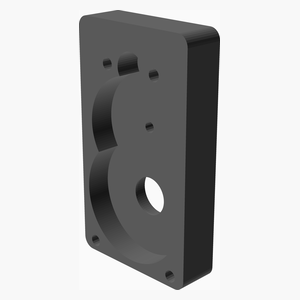
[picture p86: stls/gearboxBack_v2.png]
gearboxBack_v2.stl


### Sub-assemblies

1 x gearBox_part3_assembly

gearBox_part3_assembled

### Assembly instructions

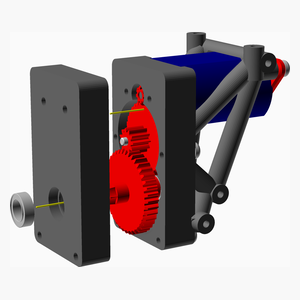
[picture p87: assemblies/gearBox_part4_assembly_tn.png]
gearBox_part4_assembly


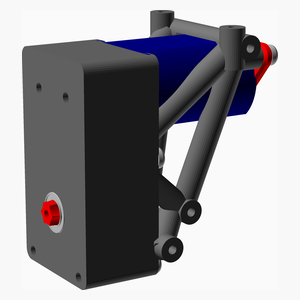
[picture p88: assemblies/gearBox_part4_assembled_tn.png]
gearBox_part4_assembled


## GearBox Part5 Assembly

### Vitamins

Qty | Description
2 | Screw M2 pan self tap x 6mm

### 3D Printed parts

2 x Center_Drive_Cup.stl

Center_Drive_Cup.stl

### Sub-assemblies

1 x gearBox_part4_assembly

gearBox_part4_assembled

### Assembly instructions

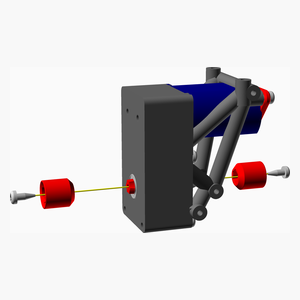
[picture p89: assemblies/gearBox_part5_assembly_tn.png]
gearBox_part5_assembly


1. Insert both Center_Drive_Cup with 2 M2 self tapping screw 6 mm.

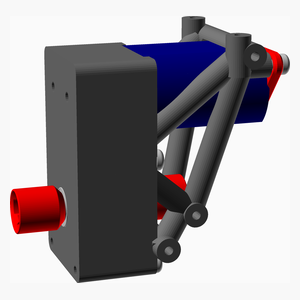
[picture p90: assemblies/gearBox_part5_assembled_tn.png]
gearBox_part5_assembled


## GearBox Part6 Assembly

### Vitamins

Qty | Description
4 | Screw M2 pan self tap x 12mm

### 3D Printed parts

1 x frameBack_v2_1.stl

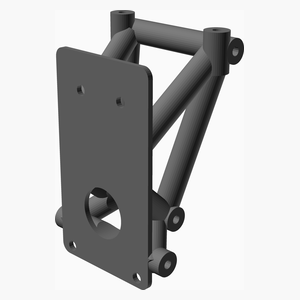
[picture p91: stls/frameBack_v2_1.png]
frameBack_v2_1.stl


### Sub-assemblies

1 x gearBox_part5_assembly

gearBox_part5_assembled

### Assembly instructions

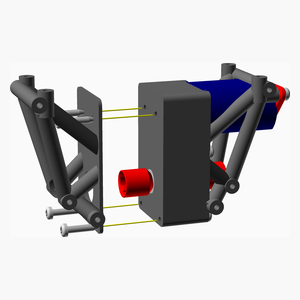
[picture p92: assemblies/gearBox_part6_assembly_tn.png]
gearBox_part6_assembly


1.Install the frameBack_v2_1 with 4 M2 self tapping screw 12 mm.

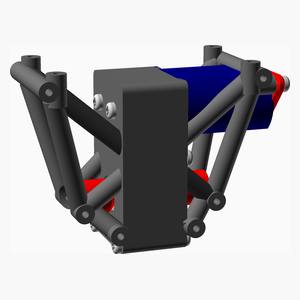
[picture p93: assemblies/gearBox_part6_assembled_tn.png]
gearBox_part6_assembled


## GearBox Part7 Assembly

### Vitamins

Qty | Description
4 | Screw M2 pan self tap x 6mm

### 3D Printed parts

1 x plate_long_v2.stl

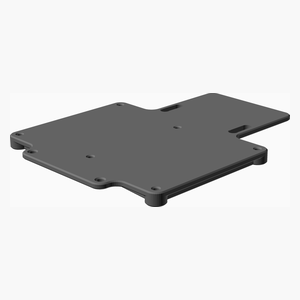
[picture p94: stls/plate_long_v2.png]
plate_long_v2.stl


### Sub-assemblies

1 x gearBox_part6_assembly

gearBox_part6_assembled

### Assembly instructions

gearBox_part7_assembly

1.Install the frameBack_v2_1 with 4 M2 self tapping screw 12 mm.

gearBox_part7_assembled

## GearBox Final Assembly

### Vitamins

Qty | Description
12 | Screw M2 pan self tap x 10mm

### 3D Printed parts

12 x 5_5_ball_Open.stl

5_5_ball_Open.stl

### Sub-assemblies

1 x gearBox_part7_assembly

gearBox_part7_assembled

### Assembly instructions

gearBox_final_assembly

gearBox_final_assembled

## Suspension Part1 Assembly

### 3D Printed parts

4 x Ball_Link_29mm.stl | 4 x Ball_Link_41mm.stl
Ball_Link_29mm.stl | Ball_Link_41mm.stl

### Sub-assemblies

2 x Axle_final_assembly | 2 x drive_shaft_assembly | 1 x gearBox_final_assembly
Axle_final_assembled | drive_shaft_assembled | gearBox_final_assembled

### Assembly instructions

suspension_part1_assembly

1. Proceed with one end at a time.
2. Install the 2 Ball_Link_41mm
3. Install the drive_shaft_assembly
4. Install the 2 Ball_Link_29mm
5. Proceed with the other end.

suspension_part1_assembled

## Suspension Part2 Assembly

### 3D Printed parts

4 x shock_43mm.stl

shock_43mm.stl

### Sub-assemblies

1 x suspension_part1_assembly

suspension_part1_assembled

### Assembly instructions

suspension_part2_assembly

1. Install the shock. Pay attention to the opening at the ball joint: they should be facing up. This will make the shock bending downward when compressed.

suspension_part2_assembled

## Main Assembly

### Vitamins

Qty | Description
4 | Screw M2 pan self tap x 6mm
4 | Screw M2 pan self tap x 8mm

### 3D Printed parts

1 x Center_Drive_Shaft_P2_15_5mm.stl | 1 x body_v3.stl | 1 x shock_46mm.stl
Center_Drive_Shaft_P2_15_5mm.stl | body_v3.stl | shock_46mm.stl

1 x wheel_26_5mm.stl

wheel_26_5mm.stl

### Sub-assemblies

1 x suspension_part2_assembly | 2 x wheel_left_assembly | 2 x wheel_right_assembly
suspension_part2_assembled | wheel_left_assembled | wheel_right_assembled

### Assembly instructions

main_assembly

1. Install the 4 wheel with M2 self tapping screw 8 mm.
2. Install the body with 4 M2 self tapping screw 5 mm.

main_assembled

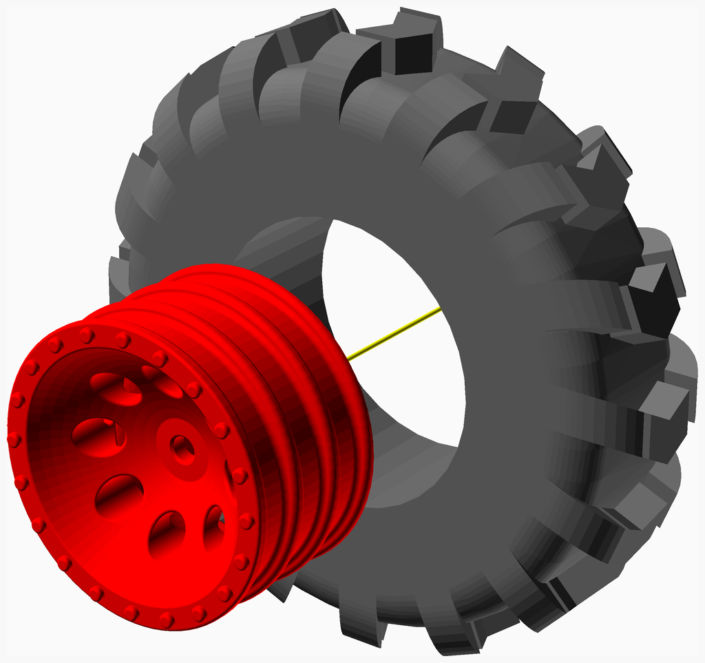
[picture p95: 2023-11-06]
assemblies/wheel_right_assembly.png

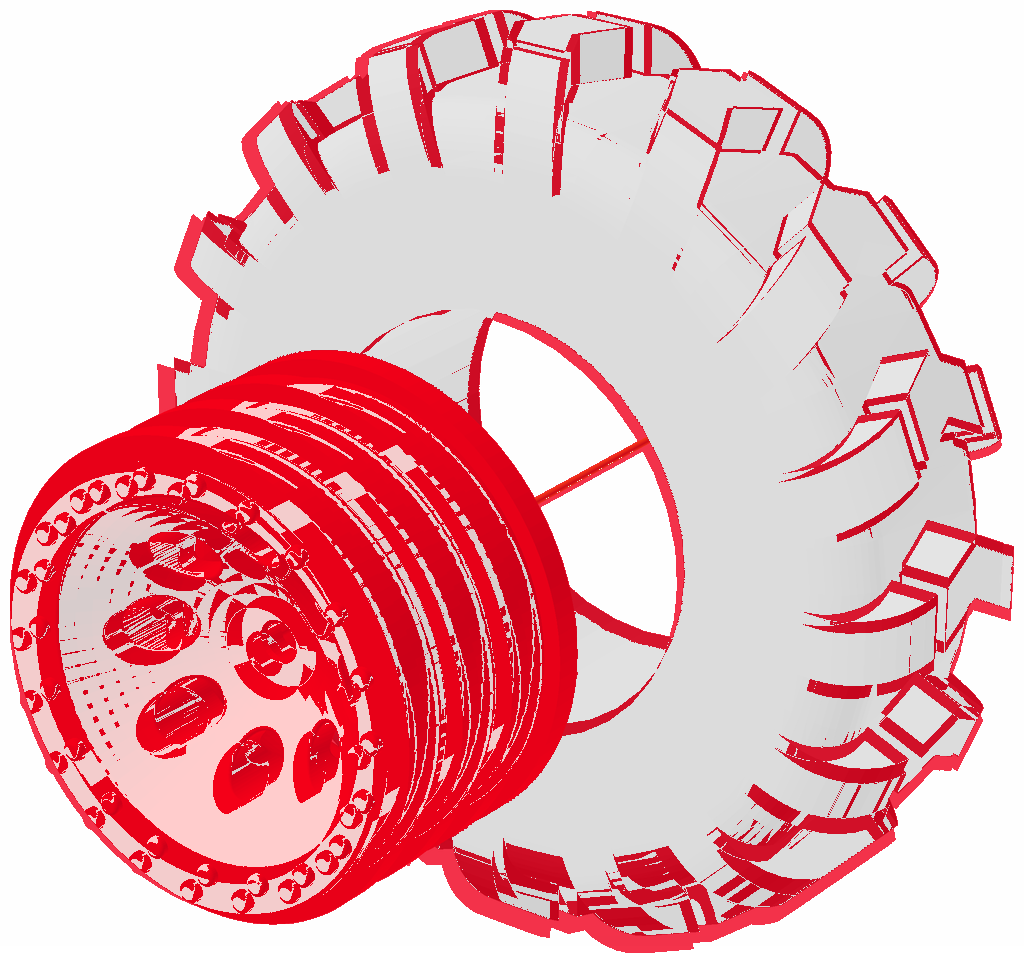
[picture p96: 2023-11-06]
assemblies/wheel_left_assembly_diff.png

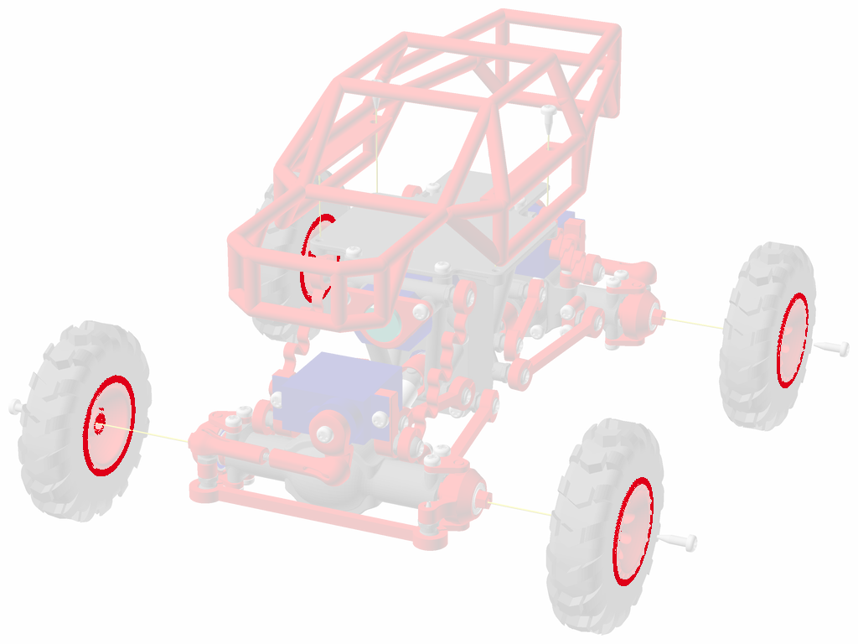
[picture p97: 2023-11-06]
assemblies/main_assembly_diff.png

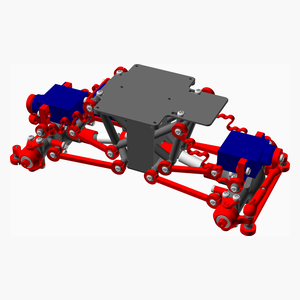
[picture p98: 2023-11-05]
assemblies/suspension_part2_assembly_tn.png

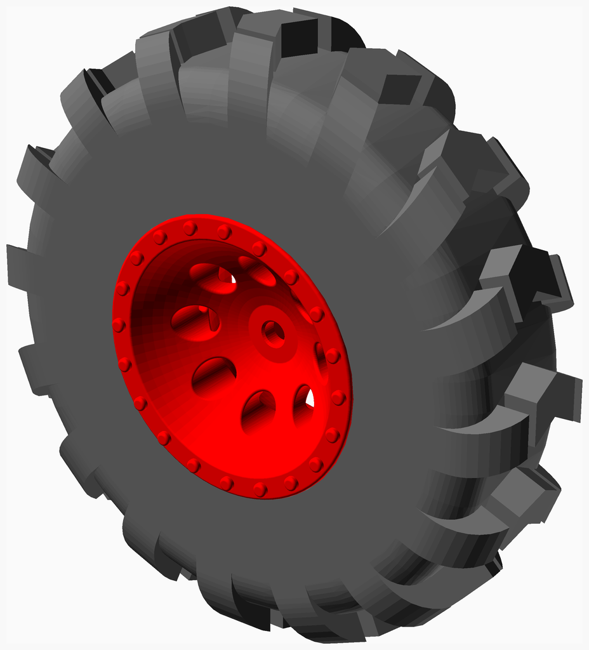
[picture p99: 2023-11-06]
assemblies/wheel_left_assembled.png

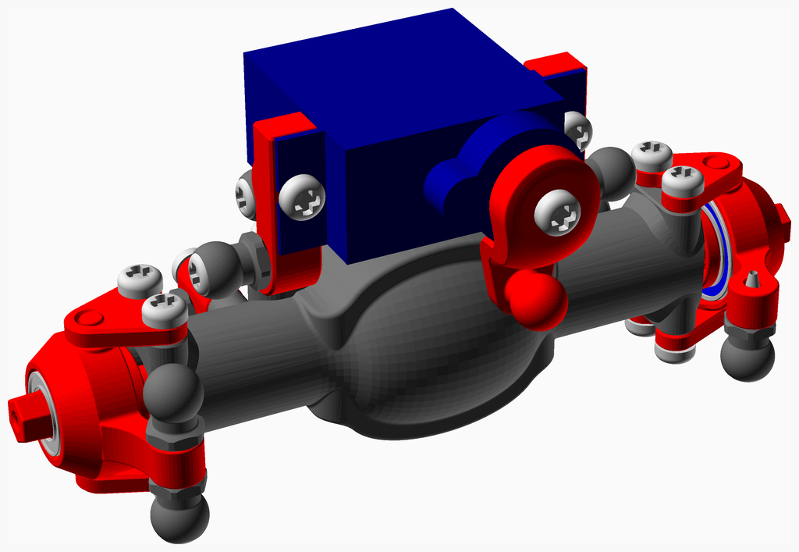
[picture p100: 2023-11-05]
assemblies/Axle_part7_assembled.png

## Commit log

2023-11-04 restructured bom
    [rockCrawler_main.scad]
2023-11-05 complete v1
    [Ball_Link_29mm.stl, Ball_Link_41mm.stl, Center_Drive_Shaft_P1.stl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]
2023-11-06 fix wheel
    [rockCrawler_main.scad]
